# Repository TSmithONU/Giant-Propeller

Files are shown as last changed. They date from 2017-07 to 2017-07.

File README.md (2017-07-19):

# Giant Propeller

Soliwords part files, Eagle files, and Arduino files

The goal of this project was
to replace the Giant
Propeller controls with a
newer and more robust
version. The old system
used a potentiometer to
control an industrial motor
controller. The problem
with the original system is
that the potentiometer was
susceptible to being over
turned and breaking. To
remedy this, an optical split
sensor is used to measure
the speed of the hand
crank. After the speed of
the crank is read, the
onboard Teensy outputs an
analog signal to an op-amp.
That op-amp signal then
controls 0-10v to adjust the
speed of the motor
controller. All this is
assembled on a custom
circuit board. This new set
up has no physical end
points which holds up
better to children. Since
install, we have calibrated
the sensitivity, but no
repairs for everyday use.

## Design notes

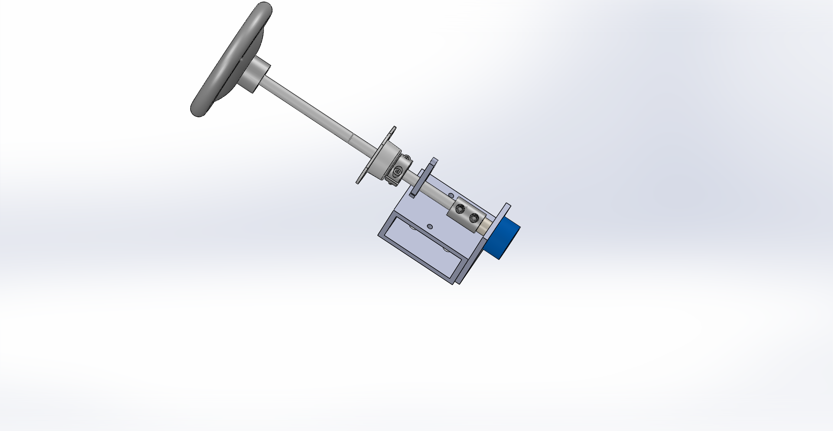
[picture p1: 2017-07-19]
Giant Prop/RotoControll.PNG

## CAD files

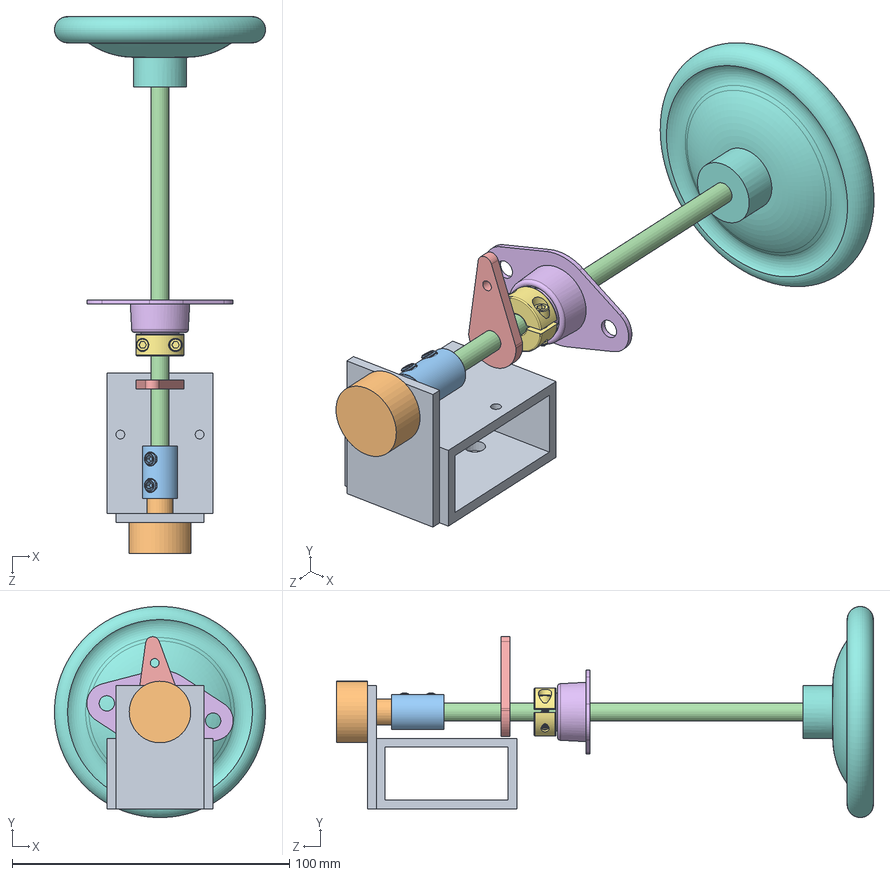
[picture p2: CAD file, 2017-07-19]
Giant Prop/RotoControll.SLDASM
76.2 x 76.2 x 193.8 mm
newBase
Pot
6412K110_BLK-OXIDE STL SET SCREW RIGID SHAFT COUPLING
1327K650_MINIATURE 12L14 DRIVE STEEL SHAFT
End Stop
1434K430_LIGHT DTY TWO-BOLT FLANGE-MOUNTED ROLLER BRNG
6436K120_TWO-PIECE CLAMP-ON SHAFT COLLAR
6024K810_SOLID CAST IRON HAND WHEEL

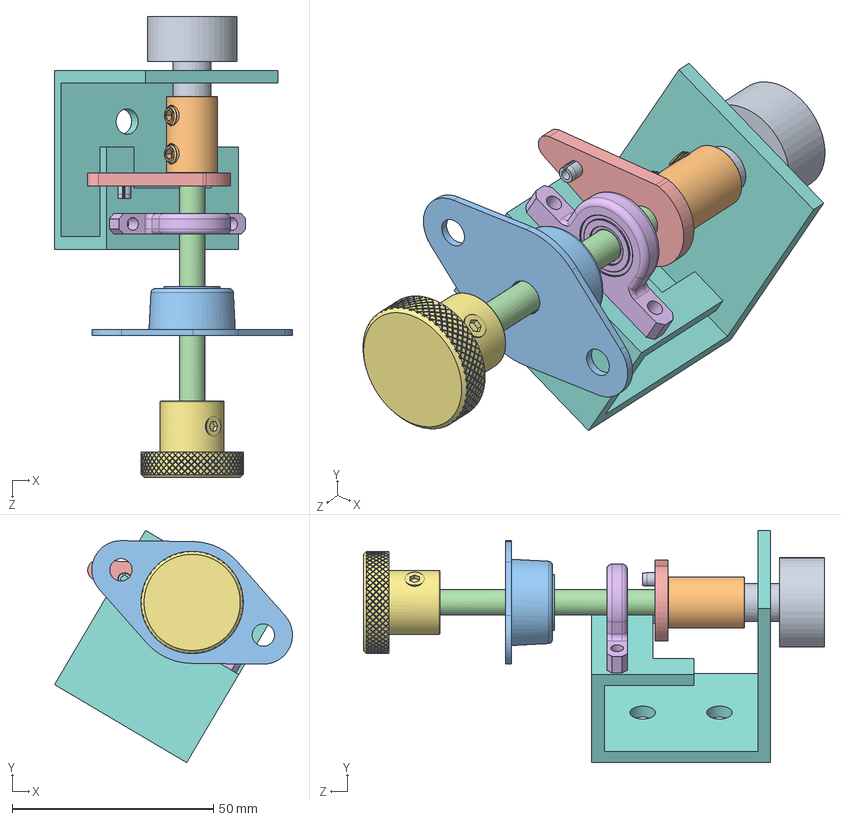
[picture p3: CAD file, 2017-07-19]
Giant Prop/KnobAssm.SLDASM
59.1 x 57.6 x 114.4 mm
Pot
6412K110
1434K430
1327K650
End Stop
8600N300
2577K210
BasePlate
92373A173

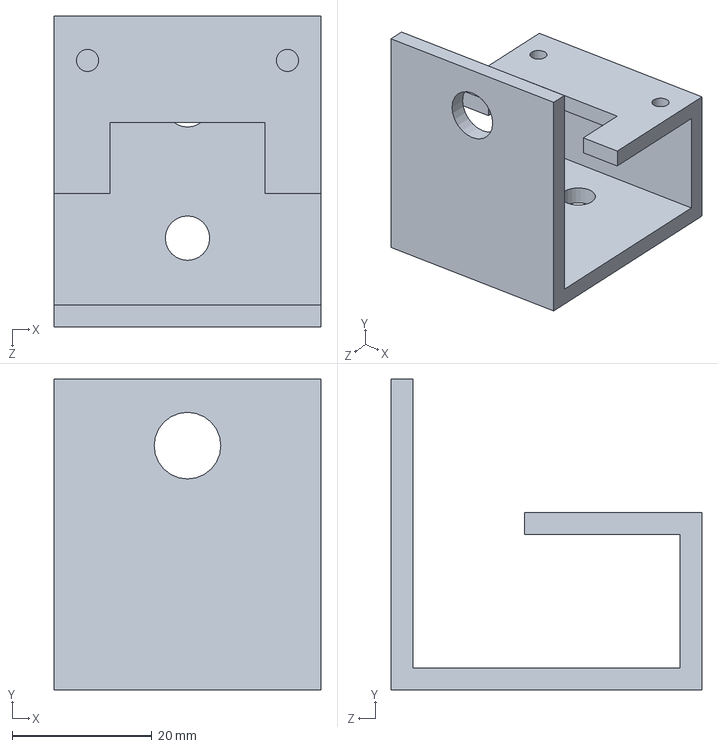
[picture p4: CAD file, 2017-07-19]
Giant Prop/BasePlate.SLDPRT
38.1 x 44.4 x 44.4 mm

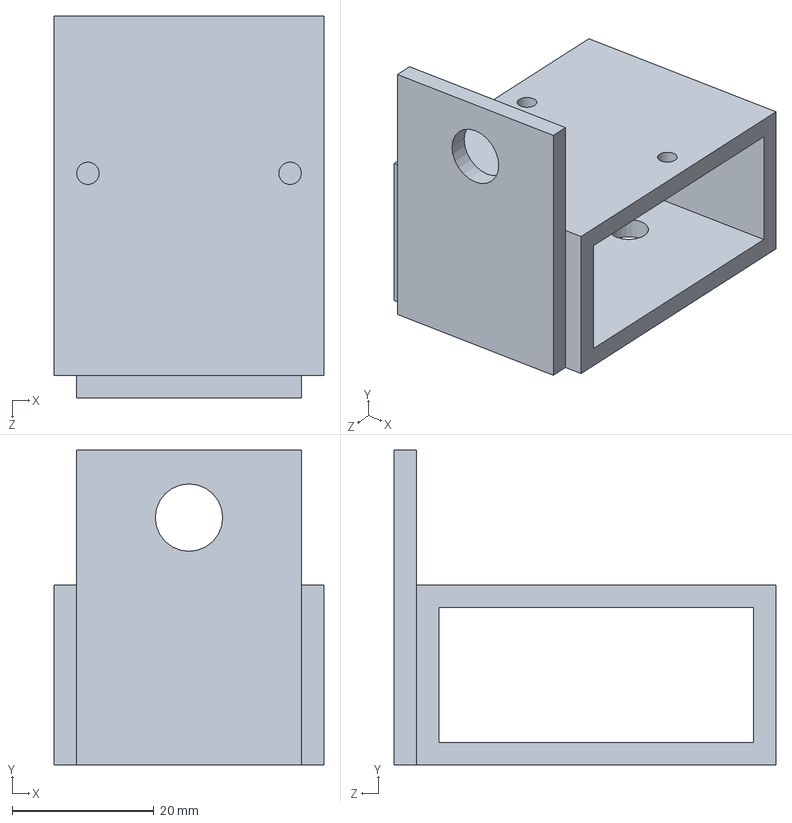
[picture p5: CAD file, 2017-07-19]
Giant Prop/newBase.SLDPRT
38.1 x 44.5 x 54.0 mm

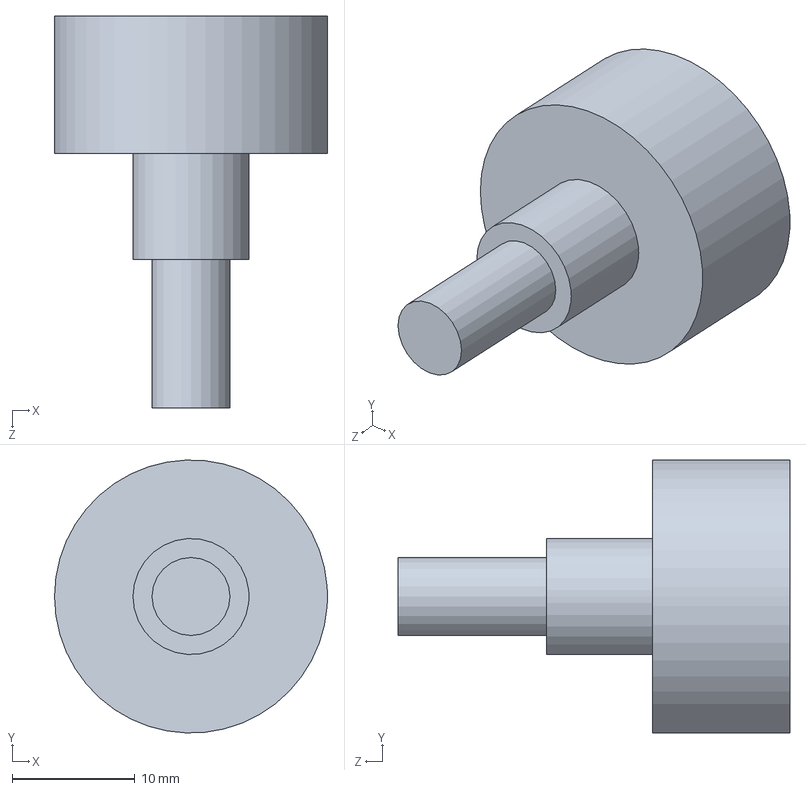
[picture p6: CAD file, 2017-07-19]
Giant Prop/Pot.SLDPRT
22.2 x 22.2 x 31.9 mm

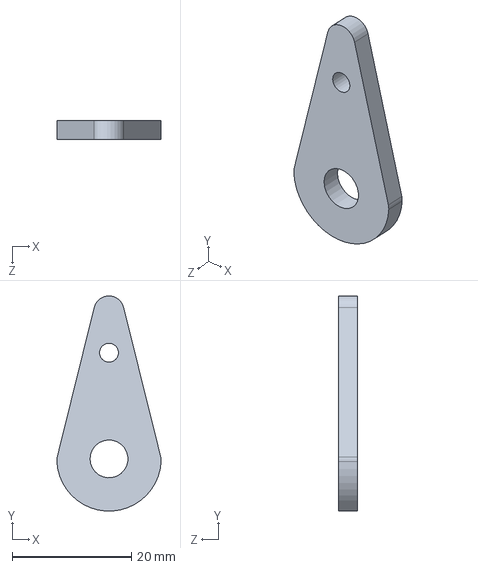
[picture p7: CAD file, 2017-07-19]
Giant Prop/End Stop.SLDPRT
17.5 x 36.1 x 3.17 mm

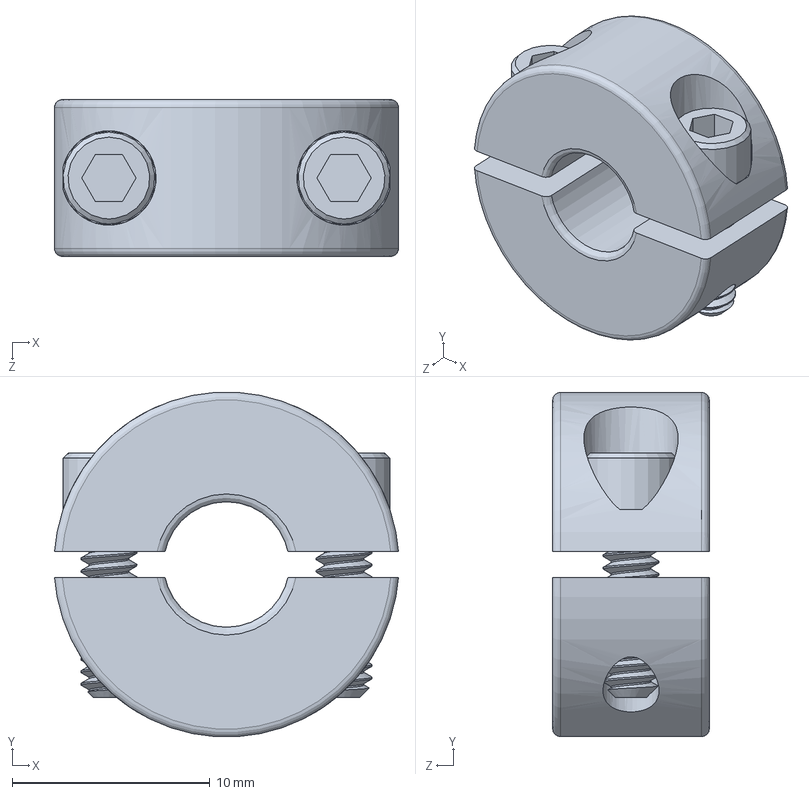
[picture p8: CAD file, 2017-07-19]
Giant Prop/6436K120_TWO-PIECE CLAMP-ON SHAFT COLLAR.SLDPRT
17.4 x 17.4 x 7.94 mm

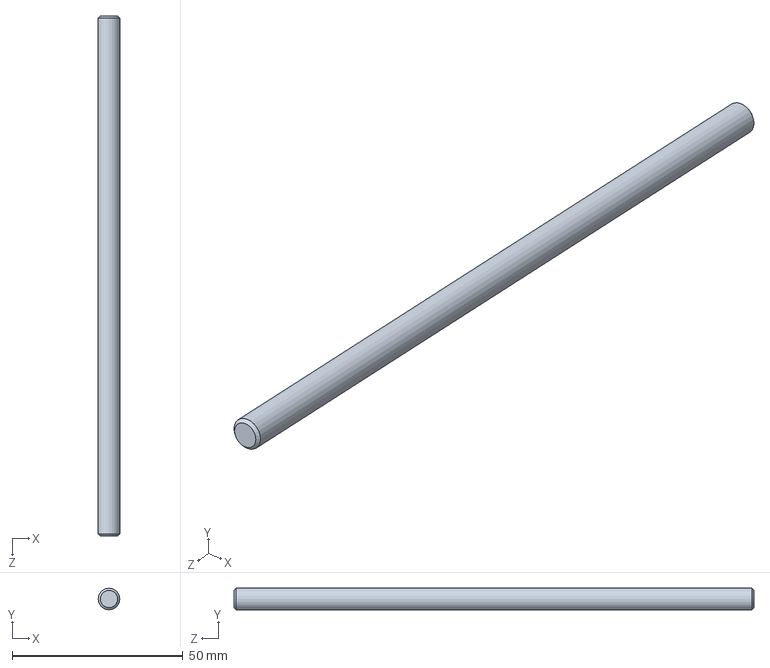
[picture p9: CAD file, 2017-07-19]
Giant Prop/1327K650_MINIATURE 12L14 DRIVE STEEL SHAFT.SLDPRT
6.35 x 6.35 x 152.4 mm

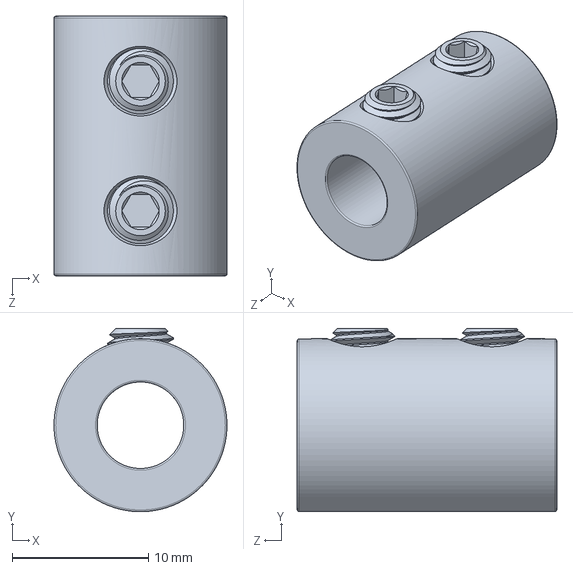
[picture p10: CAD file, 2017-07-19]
Giant Prop/6412K110_BLK-OXIDE STL SET SCREW RIGID SHAFT COUPLING.SLDPRT
12.7 x 13.5 x 19.1 mm

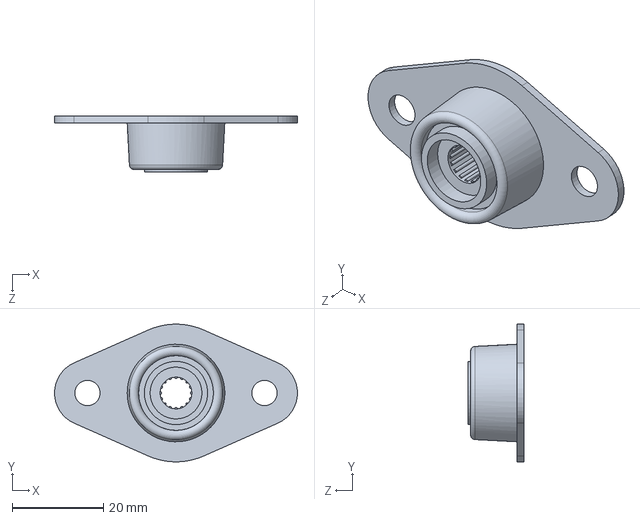
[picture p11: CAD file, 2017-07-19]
Giant Prop/1434K430_LIGHT DTY TWO-BOLT FLANGE-MOUNTED ROLLER BRNG.SLDPRT
53.3 x 30.2 x 12.2 mm

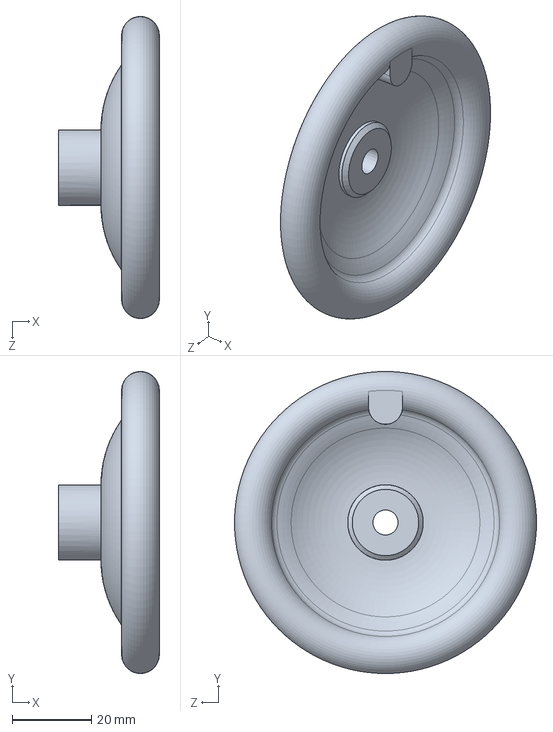
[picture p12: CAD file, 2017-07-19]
Giant Prop/6024K810_SOLID CAST IRON HAND WHEEL.SLDPRT
25.4 x 76.2 x 76.2 mm

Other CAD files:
Giant Prop/Adapter Plate.SLDPRT
Giant Prop/Adapter Plate.DXF
Giant Prop/Template.SLDDRW

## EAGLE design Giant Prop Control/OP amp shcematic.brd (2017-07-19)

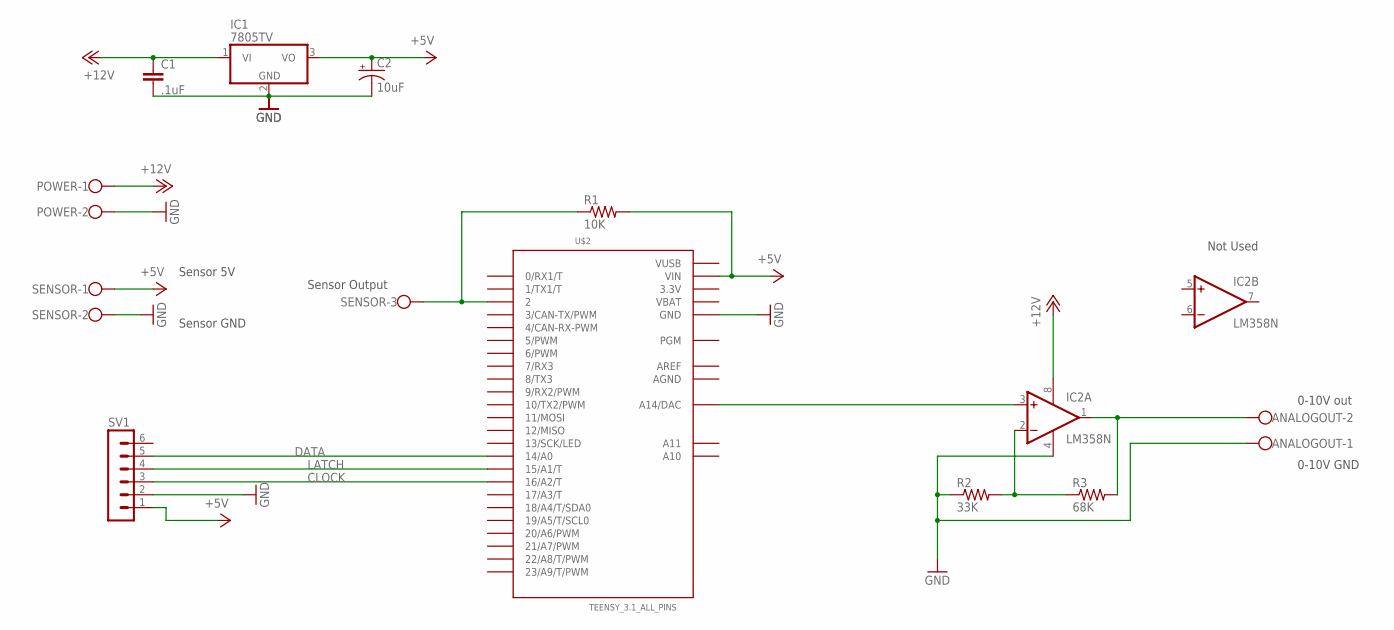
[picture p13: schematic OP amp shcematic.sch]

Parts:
ANALOGOUT: W237-102
C1: .1uF; C2.5-3
C2: 10uF; E2-4
IC1: 7805TV; TO220V
IC2: LM358N; DIL08
POWER: W237-102
R1: 10K; 0309/12
R2: 33K; 0309/12
R3: 68K; 0309/12
SENSOR: W237-103
SV1: MA06-1
U$2: TEENSY_3.1_ALL_PINS; TEENSY3-ALL_PINS

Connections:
3.3V: U$2.3.3V, U$2.3.3V1 (3.3V)
+5V: C2.+, IC1.3 (VO), R1.2, SENSOR.1, SV1.1, U$2.VIN
+12V: C1.1, IC1.1 (VI), IC2.8 (V+), POWER.1
AGND: U$2.AGND
AREF: U$2.AREF
CLOCK: SV1.3, U$2.16/A2 (16/A2/T)
DATA: SV1.5, U$2.14/A0
GND: ANALOGOUT.1, C1.2, C2.-, IC1.2 (GND), IC2.4 (V-), POWER.2, R2.1, SENSOR.2, SV1.2, U$2.GND, U$2.GND1 (GND)
LATCH: SV1.4, U$2.15/A1 (15/A1/T)
unnamed: IC2.3 (+IN), U$2.RESET/DAC (A14/DAC)
unnamed: ANALOGOUT.2, IC2.1 (OUT), R3.2
unnamed: R1.1, SENSOR.3, U$2.2
unnamed: IC2.2 (-IN), R2.2, R3.1
VBAT: U$2.VBAT
VUSB: U$2.VUSB

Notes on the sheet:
Sensor Output
Sensor 5V
Sensor GND
0-10V out
0-10V GND
Not Used

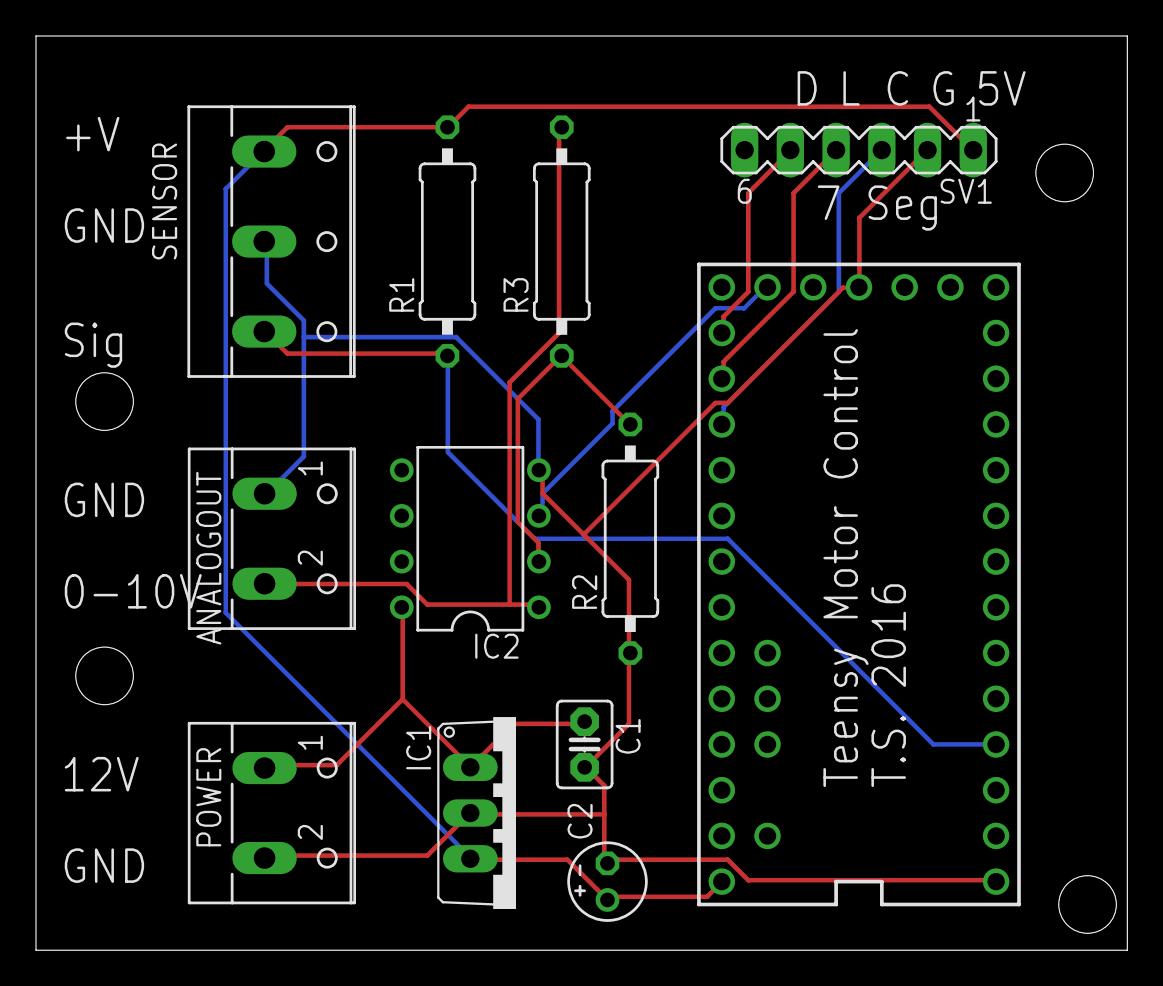
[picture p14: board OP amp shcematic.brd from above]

Board: 2 copper layers, 60.6 x 50.8 mm, 12 parts (0 on the bottom side), 11 nets.

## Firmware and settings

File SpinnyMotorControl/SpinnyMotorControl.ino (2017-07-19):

#include <Servo.h>

#include <TimerOne.h>

#define CLOCK 16
#define LATCH 15
#define DATA 14

int Numbers[10] = {B00111111,B0000110,B01011011,B01001111,B01100110,B01101101,B01111101,B00000111,B01111111,B01100111};
int x= 0;
int y= 0;
int z= 0;

unsigned int counter = 0;
#define numSpokes 1
int thresh = 115;

int revolutions = 0;
int val = 0;

void addPulse (){
  counter++;
}

void WriteDisplay(int revs){
  int number = revs;
  int temp = 0;
  temp = number/100;
  int x = temp;
  number-=temp*100;
  temp = number/10;
  int y = temp;
  number-=temp*10;
  int z =number;

  digitalWrite(LATCH,LOW);
  shiftOut(DATA,CLOCK,MSBFIRST,byte(Numbers[z]));
  shiftOut(DATA,CLOCK,MSBFIRST,byte(Numbers[y]));
  shiftOut(DATA,CLOCK,MSBFIRST,byte(Numbers[x]));
  //shift
  digitalWrite(LATCH,HIGH);
}

void timerIsr(){
  Timer1.detachInterrupt();
  Serial.print("Wheel Speed: ");
  revolutions = (counter / numSpokes);
  WriteDisplay(constrain(map(revolutions,0,thresh,0,100),0,100));
  Serial.print (revolutions, DEC);
  Serial. println( " Revolutions per second");
  val = map(revolutions,0,thresh,0,4096);
  counter = 0;
  Timer1.attachInterrupt(timerIsr);
  
}

void setup() {
  // put your setup code here, to run once:
  Serial.begin(9600);
  analogWriteResolution(12);
    pinMode(CLOCK, OUTPUT);
  pinMode(LATCH, OUTPUT);
  pinMode(DATA,OUTPUT);

  digitalWrite(CLOCK,LOW);
  digitalWrite(LATCH,HIGH);

  pinMode(2,INPUT);


  Timer1.initialize(1000000);
  attachInterrupt(2,addPulse,RISING);

  Timer1.attachInterrupt(timerIsr);
}

void loop() {

  analogWrite(A14,(int)val);
  // put your main code here, to run repeatedly:
}
